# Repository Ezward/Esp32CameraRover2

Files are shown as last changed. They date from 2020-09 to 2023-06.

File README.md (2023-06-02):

# EzRover

- [Description](#description)
- [Status](#status)
- [The Software](#the-software)
    - [Rover Firmware](docs/rover_firmware.md#the-rover-application)
    - [Web Application](docs/web_client.md#the-web-client)
      - Here is a [video](https://youtu.be/yN2ya2mlBNU) that describes the web application.
- [The Hardware](docs/building_the_rover.md#building-the-rover)
- [Todo](docs/todo.md#todo)
- [Tags](docs/tags.md#tags)
- [Setup](#setup)

## Description
EzRover is not a sketch; it is a framework for powering cheap, capable and extensible differential drive robots.

The repository includes a C++ application that runs on the rover and a JavaScript web application that is served by the rover and is used to command the rover and to receive and visualize video and telemetry.  

The framework implements important robot primitives in the C++ application such as a websocket command protocol, closed loop speed control, pose estimation and go to goal behavior.  These primitives are implemented in C++ and run on the rover so they run fast and with low latency.

In addition, the rover serves it's own JavaScript web application which is used to calibrate and command the rover and to visualize video and telemetry from the rover.  The JavaScript web application is a distinguishing feature of this framework.  It can be used to extend the rover's capabilities using a friendly programming language (JavaScript) and powerful technologies like OpenCV.js and Tensorflow.js.

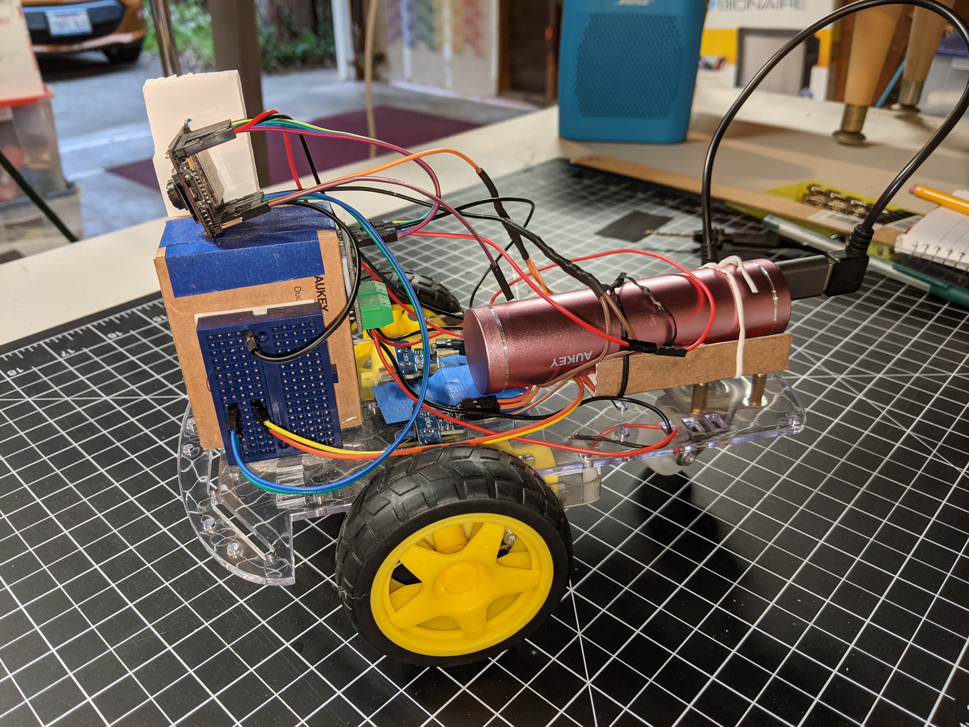
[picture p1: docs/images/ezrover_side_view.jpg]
EzRover side view


This repository includes the parts list and a set of instructions for building an inexpensive differential drive robot using an ESP32Cam micro controller, an inexpensive motor controller and a commonly available Robot Car chassis.  The result is a cheap, capable, extensible robot that can be used by hobbyists or in school settings for experiencing and learning about robotics.
- Sub-$40 bill of materials, no 3D printing and little or no soldering
- Closed-loop motor control, pose estimation, go to goal and path following.
- Remote control using a First Person View video streaming and game controller or mobile phone
- Extensibility via JavaScript, OpenCV and Tensorflow

So two important requirements are:
- The robot must be inexpensive
- The robot must be easy and safe to build

The capabilities listed above then create some other requirements;
- The robot must have it's own battery so it can operate remotely and untethered.
- The robot must have a camera to enable a first persion view for the remote operator and as a sensor for autonomous navigation.
- The robot must have odometry (using wheel encoders) for precise control of speed, trajectory and distance.
- The robot must have wifi communication to enable effective remote control from a computer or cell phone.

The chassis for the robot is a very commonly available kit that includes two dc motors, two wheels, a caster wheel and a clear plastic chassis/platform to mount everything on.  Construction is very simple.  The only soldering required is to attach 2 wires to each of the 2 motors and there are even ways of avoiding that.  

The other nice thing about these kits is that they come with wheel encoder disks; we can add two optocouplers to enable precise odometry for the robot, which is important in a number of scenarios.

The Esp32 Cam was chosen because it is a very inexpensive microcontroller that includes a camera, bluetooth and wifi.  It also comes with the header pins pre-soldered, which eliminates the need for a lot of soldering.  This is nice for beginners and for scenerios where a hot soldering iron is undersirable.  

Wiring of the robot is done using inexpensive and easy to find jumper wires with pre-crimped dupont connectors.  For the most part, we have chosen components that have pre-installed header pins so we can just connect to them using these pre-fabricated jumper wires.  This makes wiring primarily solderless.  The possible exceptions to this are the dc motors.  Each motor has two terminals that need wires connected. It turns out that soldering lead wires to such terminals is really easy, even if this is your first time using a soldering iron.  If the robot is to be assembled in a class room setting, then the wires could be pre-soldered by a teacher.  However, there are alternatives; motors can be purchased that have the lead wires presoldered.  These tend to be a little more expensive are are rarely found in a complete kit, but they can be purchased separately.

## Videos
Here a some videos that show the EzRover and web application is action:
- [EzRover 01 Introduction](https://youtu.be/yN2ya2mlBNU)
- [EzRover 02 Calibration](https://youtu.be/ciDCUUx8MXI)
- [EzRover 03 Go to Goal](https://youtu.be/_eKCqswX5D0)
- [EzRover 04 Go to Goal](https://youtu.be/TjE9ceNOTJE)

## Contributing
There are lots of ways to contribute to this project.  First, clone the repo and try it out.  If you have ideas for cool features please add a Feature Request to issues; I really want to know how you would like to use this project.  If you build the project and find any bugs, please add a bug issue.  If you want to add to the code or fix a bug, please clone the repository and make a pull request.  If you like robots and JavaScript, please star this repository; that will help us a lot.  Thanks!

## The Software
The rover software is really two big pieces; 
- The [rover code](docs/rover_firmware.md) that controls the motors and the camera runs in the ESP32 microcontroller is written in C++ (Arduino flavor).
- The client [web application](docs/web_client.md) that is used to drive the rover and view camera video runs in a browser and consists of an html file, a few css files and many JavaScript files.  

This is not a sketch; it is a framework.  It is a framework for powering cheap, capable, and extensible differential drive robots.

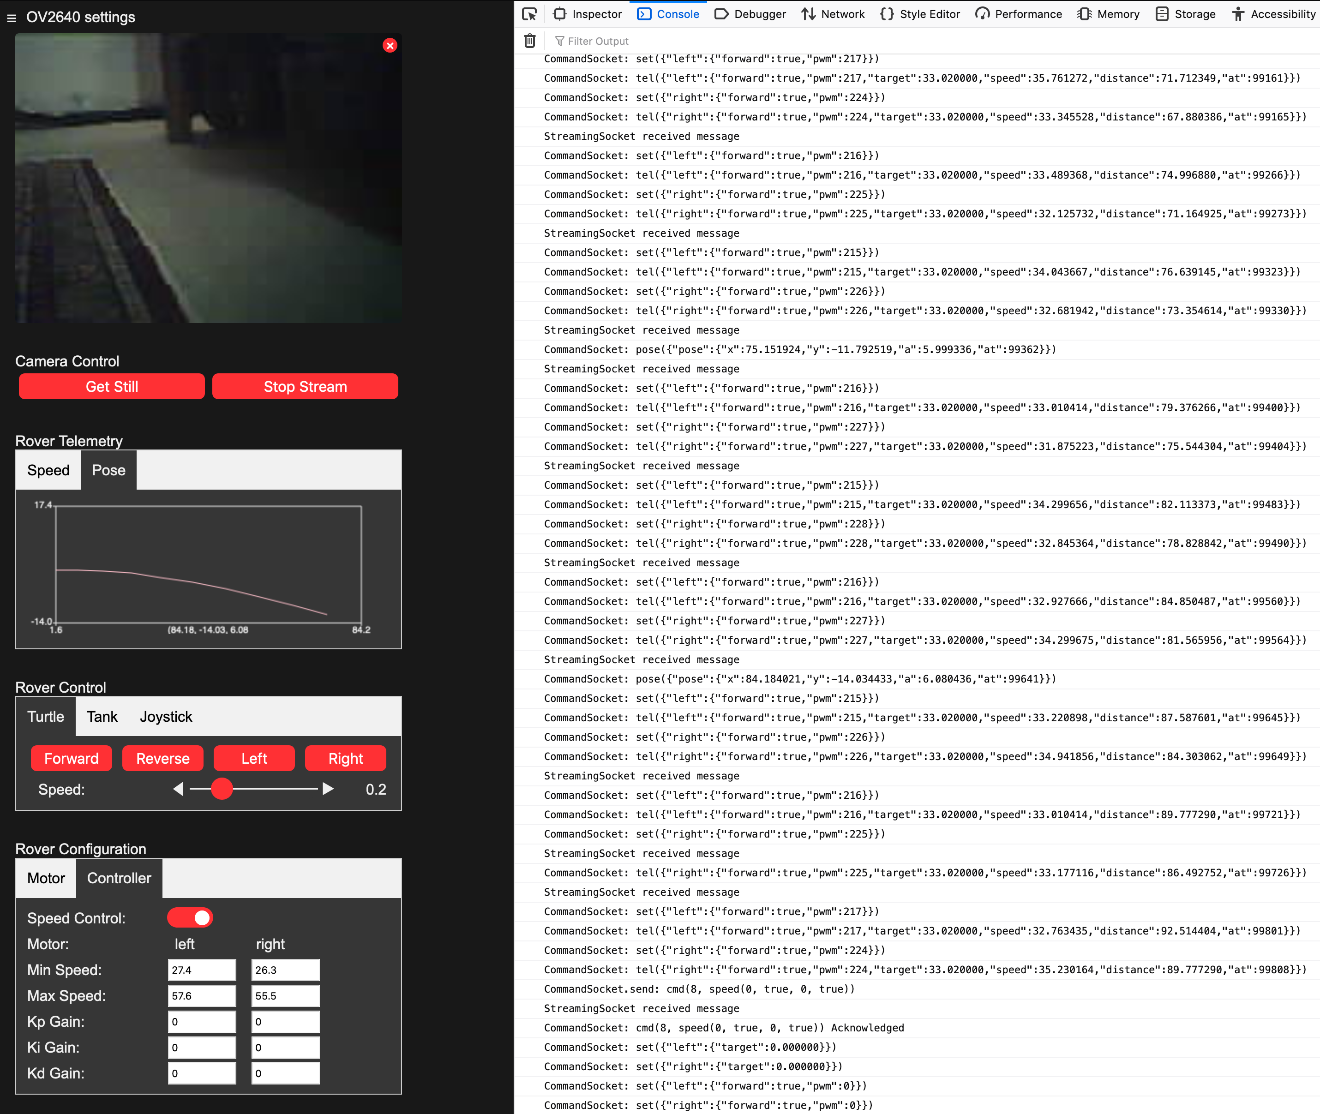
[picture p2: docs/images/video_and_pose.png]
Rover application showing video and pose telemetry


## Status
Latest code has a pretty nice web ui and decent closed-loop speed control and go-to-goal behavior.  My thinking on the project and where it can offer value or provide a differentiated capability has evolved.  Originally I wanted to create the lowest-cost robot capable of competing in a [DIYRobocars](https://diyrobocars.com/) race.  The current [Minimum Viable Racer](https://diyrobocars.com/2018/11/23/updated-minimal-viable-racer-to-use-latest-openmv-linear-regression-code/) is based on the OpenMV Cam, which is a super-nice intelligent camera with onboard compute.  A Minimum Viable Racer would cost a little under $100 to build.  I think this project could be used to create a MVR for about $40.  I still think that is true, but think there is another place we can get to that offers a broader value.  I think this project can become a cheap robot platform that provides solid primitives (speed control, pose estimation, go to goal, command protocol, telemetry and camera streaming) in a self-hosted web application that is extensible in JavaScript.  Cheap, Capable, Extensible.  

### Cheap
This project specifies a hardware BOM that is easy to get, easy to assemble and **costs under 40$** USD.  It does _not_ require a 3D printer.  It can be built with minimal or no-soldering.

### Capable
Ultimately, I would like this project to enable autonomous robotic capabilities.  It is common to see inexpensive robots based on an Arduino Uno or Nano and the same or similar rover chassis and motor controller as this project uses.  These are basically the same cost to build as this project.  They may add a set of IR sensors and provide a line-following behavior.  Or they may provide an ultrasonic sensor and provide an obstacle-avoidance/random-walk kind of behavior.  Sometimes they will provide a bluetooth adapter and a mobile app so the robot can be driven by the user with a mobile phone.  These are all good robots and I would recommend building one or another.  However, none of these are truly autonomous; the line following robots require that you draw lines for them, the obstacle-avoidance robots don't know where they are or where they are going; they just avoid stuff, and the remote control robots require you to drive them.  Autonomous robots require more capable sensors and must be able to estimate and control their position.

- **Camera**: In it's simplest use, streaming video from the camera allows the rover to show a First Person View, FPV, and facilitates remote teleoperation capability.  When combined with computer vision algorithms, a camera equipped robot can execute many autonomous behaviors; line following, lane keeping, obstacle detection, image recognition, camera SLAM and many more.  

- **Wheel Encoders**: integration of wheel encoders for feedback and a kinematic model enables 3 important robot capabilities:
  - speed control: precisely control the speed of the rover under program control
  - pose estimation: understand the position and orientation of the robot as it moves
  - go-to-goal behavior: navigation to a specific location under program control.
- **Wifi** and **web** connectivity: This allows the robot to be controlled over the web; commands can be sent and telemetry can be received.  This is the key to extensibility.
  - command protocol
  - rover telemetry

### Extensible
It's not a sketch, it's a framework for differential drive robots. 

The basic capabilities of the rover are built-in; speed control, pose estimation, go-to-goal behavior.  Those are written in C++ and execute directly on the rover's microcontroller.  Because we have chosen a microcontroller with WIFI and HTTP, the robot can self-host it's own web application and user-interface. This is where a lot more capability can be added in an easy to use language; JavaScript.  Since the rover serves it's own web application, the robot can be run without the need to install a separate client application; just open the application in any browser on a computer or mobile phone.  The application is written in it's own framework with minimal required dependencies so it is very easy to build and debug using standard browser development tools.  

The rover web application can send commands to the rover and it can receive telemetry from the rover so it knows the rover's state.  It allows the rover to be driven by keyboard, game controller or algorithmic control.  There is a graphics library that plots telemetry and position in real-time.  Detailed telemetry can be viewed in the browser's console.  The rover can also stream video from the camera to the rover application.  With powerful JavaScript libraries, like OpenCV.js and Tensorflow.js, computer vision and deep learning algorithms can be run against the camera input.  By leveraging the built-in speed control, pose estimation and go-to-goal primitives, higher-level behaviors can be created like goal selection, path planning, sign-recognition and real-time obstacle detection and avoidance; the building blocks of an autonomous vehicle. 

- Self-hosted **web application**
- Extensible with **Javascript**
  - **OpenCV**.js
  - **TensorFlow**.js
- Debuggable: since much of the robot's code is in JavaScript, the browser's **development tools** can be used to debug.

#### Useful Extensions
These would be great things to add to the the JavaScript application.
- OpenCV.js camera calibration
- OpenCV.js camera line following
- Camera lane keeping (OpenCV.js or TensorFlow.js)
- Path representation and Pure Pursuit path following
- Map representation and path planning
- Traffic sign and traffic light recognition (TensorFlow.js)
- Obstacle recognition and avoidance (Tensorflow.js)

### What would you like to see?
- Add an enhancement request to the github issues.  That can begin the discussion.  It would be great to know how you want to use the rover.
- Before you add a new issue, please search the current issues to see if there is one that covers your concern.  If there is, add to that discussion.  Thanks.

## Setup
I'm using Visual Studio Code and the Platform I/O plugin for embedded development.  It's nice because it can handle the C/C++ code and the HTML/CSS/JavaScript code all in one IDE.
- Install Visual Studio Code: https://code.visualstudio.com/
- To get type-checking of JavaScript in Visual Studio Code (code is JavaScript with JsDoc that can be type-checked):
  - Install nodejs: https://nodejs.org
  - Install TypeScript: https://www.typescriptlang.org/download
- Install Platform I/O into Visual Studio Code: https://platformio.org/platformio-ide
- git clone the repo to your local machine
- open the cloned project folder in Visual Studio Code

See [Rover Firmware](docs/rover_firmware.md) for a detailed explaination of setup and code building.

NOTE: Currently I do not have a Windows batch scripts that are equivalent to the Bash shell scripts in the tools folder that are used to bundle the client assets into the rover firmware.  You could do this in a Linux shell if you have installed Linux Subsystem for Windows.  It may also work in the Git for Windows shell or Cygwin. You can also run a VM.  https://itsfoss.com/run-linux-commands-in-windows/  Lastly, if you create equivalent batch scripts, please think about opening a pull request so the community can use them.  Thanks.

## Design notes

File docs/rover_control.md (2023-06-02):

## Rover control
Controlling (driving) the rover is done with the web application.  There are 4 control modes;
- ***Turtle Control*** : This is is like a Logo 'turtle'; you can move forward, backward, turn left and turn right.  This is done with 4 buttons in the web UI.
- ***Tank Control*** : In this mode, each wheel is controlled separately and can go forward or backward.  This is done using a connected game controller and two of the analog axis, one for each wheel (see how to connect a game controller to your browser below).
- ***Joystick Control*** : In this mode, the rover is controlled with one analog joystick (or one for steering and one for throttle) using a connected game controller (see how to connect a game controller to your browser below). 
- ***Go to Goal*** : In this mode, you provide an (x,y) position and the rover drive's itself there and stops.

- TODO: document how to get wifi address of ESP32 (turn off wheel encoders and get address from serial monitor; use wifi router to fix rover's DHCP ip address in the router)

### Turtle Control 
In 4-button Turtle control mode, the rover has 4 movement commands; forward, turn left, turn right, and reverse.  The speed command sets the speed of the motors.  So when a direction command is given, the speed is based on the most recent speed command.  Finally there is the stop command, which will stop the motors.  
- forward
- turn left
- turn right
- reverse
- stop
- speed

Here is a video that demonstrates [Turtle mode](https://youtu.be/yN2ya2mlBNU) control.

Turtle Control is simple to understand and makes it easy to plan a route; it can also be implemented simply with UI buttons or a keyboard.  The left-turn and right-turn commands are really 'spin' commands; the rotation is around the center of the robot, between the two wheels.  If effect, it is like a 'turtle graphics' kind of control.  So Turtle control mode allows the bot to go forward or backward in a straight line and to spin left or right.  Smooth turns are not really possible, but must be broken up into short strait lines connected with small turns (like approximating a circle with a polygon).

The browser application provides 4 buttons in the UI to send these commands to the rover.  When a direction command is sent by clicking a direction button in the browser application, the command is sent and the button turns to a 'stop' button and the other 3 direction buttons become disabled until the 'stop' button is pressed.  This makes it visual obvious that the user should send a 'stop' command between movement commands.

In addition, the browser application binds the arrow keys on the keyboard of a desktop or laptop or Chromebook to send these commands to the rover.  The arrows keys are mapped as you might expect; up-arrow = forward, left-arrow = turn left, right-arrow = turn right, and down-arrow = reverse.  The application code always inserts a stop command between movement commands to make sure there is no attempt to change direction dramatically (like directly from full forward to full reverse) that has the possibility of damaging the motor's gears.

This is the default mode and works with any desktop or mobile browser.

### Tank Control
In tank control mode, each motor is controlled separately and can go either forward or backward with a specified speed.
- left forward/reverse
- right forward/reverse

This mode is meant to be used with a gamepad that has at least two analog joystick controls, like an XBox One controller or a Playstation 2, 3, or 4 controller.  Typically the left joystick's vertical axis would be used to drive the left wheel; push forward to turn the wheel forward, pull back to turn the wheel backward.  The speed of rotation is determined by how far the stick is moved.  Similarly, the right joystick is generally used to control the right wheel.

Because of the analog nature of the controls, much smoother movements can be created using this mode.

Tank control is enabled when a gamepad with at least two joysticks is connected to the computer that is running the browser application and a button or joystick on the gamepad is pressed or moved.

### Joystick control
In joystick control mode is meant to be used with a gamepad that has at least one analog joystick (the existence of 2 'axes' is assumed to mean one joystick).  One axes controls the forward/reverse speed (push forward to go forward, pull back to reverse) and the other axes controls turning (push left to turn left, push right to turn right).  The speed is determined by how far the joystick is pushed forward or backward and the angle or the turn is determined by how far the joystick is moved left or right.
- forward/reverse
- left/right

Joystick mode is perhaps the most natural driving mode.  

Note that it is also possible, on a gamepad with two analog joystics, to map the vertical axis of one joystick for forward/reverse and the horizontal axis of the other joystick for left/right turns.

Joystick control is enabled when gamepad with at least one analog joystick is connected to the computer that is running the browser application and a button or joystick on the gamepad is pressed or moved.

### Browser Gamepad support
Tank Control and Joystick Control require a gamepad connected to the machine running the browser application. Detection of the gamepad controller and configuration of the axes is done using the HTML5 gamepad API.  To make this mode available, you must first connect a gamepad controller that has at least one analog joystick for Joystick Control or two analog joysticks for Tank Control (actually, the existence of 2 'axes' is assumed to be a joystick, so 4 axes is assumed to be two joysticks).  Note that after the gamepad is connected to the computer, you must press a button or move a joystick before it is detected by the browser.

This has been tested on the latest Chrome and Firefox 77.01
- Firefox 77.01 on MacOS Catalina 10.15.5
- Chrome 83.0.4103.116 on MacOS Catalina 10.15.5

It appears the Apple Safari does not support the HTML5 Gamepad API.

### Go To Goal
In Go To Goal mode, you input an (x,y) position and the rover drives to that position and stops.  Accuracy depends upon good calibration of motor stall PWM, minimum speed and maximum speed for each wheel.  This capability distinguishes this rover from most other super-cheap rovers.  This is also implemented as a command that can be sent to the rover using JavaScript, and telemetry is returned that tells the web applcation when the goal is achieved.  Once you are ready to start hacking the rover's web applcation, you can use this basic behavior and string many together to get the robot to do more complex behaviors.

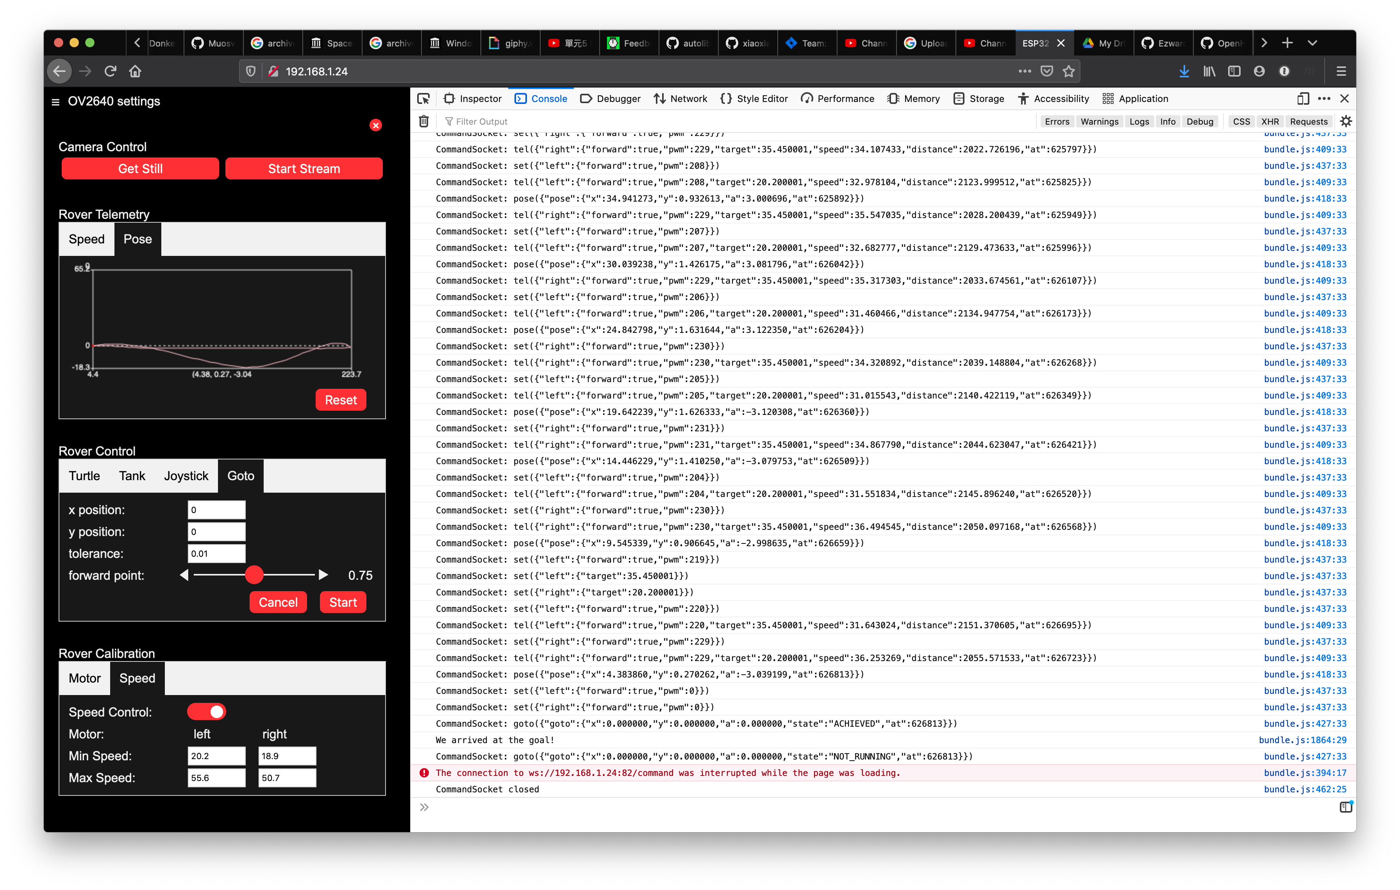
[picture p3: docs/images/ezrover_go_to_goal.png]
EzRover Go to Goal Telemetry


Here is a video that demonstrates the [Go to Goal behavior](https://youtu.be/_eKCqswX5D0) in action.  Here is another with side-by-side video of [EzRover and the telemetry](https://youtu.be/TjE9ceNOTJE) on the web application.

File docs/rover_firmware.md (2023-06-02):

## The Rover Application
The rover code (this is what I'll call the code that runs on board the ESP32) runs in the ESP32 Cam microcontroller.  It is written in Arduino flavor C++.  It includes 3 big pieces of functionality;
- The web server code
- The camera code
- The rover code

***The ESP32 Application Structure***
- WebServer - handle camera configuration requests
- Streaming Server - receive rover commands, stream image frames
- Camera - configure and read frames from the ESP32 Camera
- TwoWheelRover
    - CommandProcessor - parse rover commands and execute them on the rover.
    - DriveWheel x2
        - Motor - send control signals to the motor via a L9110s motor controller board
        - Encoder - read wheel revolutions using optical-interrupter board
        - SpeedController - control wheel speed using a software PID controller
    - Pose Estimator - continually update the rover's idea of it's position and orientation as it moves.
    - GotoGoal Behavior - Use speed control and pose estimation drive the rover to a given (x,y) position

Much of the camera code in `src/camera` is adapted from the ESP32 Cam `CameraWebServer` demonstration sketch provided with the ESP32 Cam Arduino framework.  It would be worth your time to get that demo application running on your ESP32 Cam before you attempt to build the rover and run the rover application.  That will give you the opportunity to learn how to install the necessary libraries and how to upload programs to the ESP32 Cam via a USB-to-Serial adapter board.  I recommend the [article](https://dronebotworkshop.com/esp32-cam-intro/) and [video](https://www.youtube.com/watch?v=visj0KE5VtY) from The Dronebot Workshop.  He provides an excellent, thorough description of how to setup the software and upload and run the demonstration script.  NOTE: after showing how to run the demonstration sketch, he goes into a section of how to add an external antenae to the ESP32 Cam; you do NOT need to do that for this project.

NOTE: On startup the rover tries to connect to a wifi router using the credentials in the file `wifi_credentials.h`.  That file is NOT checked into the project source.  You will need to create one for yourself that provides credentials to your wifi router.  It is recommended that you do NOT check this into source control.  See the next section, Compiling the Firmware, for the format of `wifi_credentials.h`.

### Compiling the Firmware
See [Firmware Toolchain](./software_setup.md#firmware-toolchain)

This is detailed in in [Firmware Toolchain](./software_setup.md#firmware-toolchain) but it is worth mentioning again here.  The rover needs to compile in the wifi credentials for the wifi it will be operating in.  This is done by putting them in header file that gets included in the compile.
- Create a `wifi_credentials.h` in the `src/` folder - You must add your wifi credentials to this file.  Do NOT check this file into source control.  It should look like this;
```
const char* ssid = "yourwifi";
const char* password = "yourpassword";
```
- Now you can compile the firmware by selecting the check-mark on the toolbar at the bottom of the Visual Studio Window.

### Downloading the Firmware to the Rover
The ESP32Cam has very few available GPIO pins, so the output of the wheel encoder LM393 Optocoupler modules use the Serial TX/RX pins.  That means, in this hardware configuration, we cannot use serial output and wheel encoders at the same time.  So when downloading the firmware to the ESP32, we must disconnect the wheel encoder outputs and connect a USBtoSerial converter.  Once the download is complete, you can disconnect the USBtoSerial converter and reconnect the wheel encoder outputs.  In my prototype, I used a mini-breadboard as a switch-board for this purpose so I did not have to continually disconnect/reconnect dupont wires to the ESP32Cam.  Instead, I use a pair of wires to connect the TX/RX to a mini-breadboard and a pair to the USBtoSerial board and a pair to the wheel encoder outputs.  I connect the the USBtoSerial pair when downloading the firmware.  I connect the wheel encoder pair when I want to run the rover.

- Here is a good video from the Dronebot Workshop which includes a section on how to [download firmware to the ESP32Cam](https://youtu.be/visj0KE5VtY?t=429) 
- To use the serial TX/RX pins for downloading firmware, you must detach the encoder output wires from those pins and connect a USBtoSerial converter (make sure to use a 3.3v serial converter).  The Esp32Cam TX pin (gpio-01) must be connected to the RX pin on the USBtoSerial converter.  The Esp32Cam RX pin (gpio-03) must be connected to the TX pin on the converter.  Connect the GND pin on the converter to a common ground with the Esp32Cam.  Do NOT connect the output voltage from the converter; the converter is powered by the USB connection
- To put the Esp32Cam into programming mode you must also tie gpio-0 to ground.
- Once you have connected the USBtoSerial converter to the TX/RX pins (and to power and common ground), and connected gpio-0 to ground, then you must restart the Esp32Cam so it enters programming mode.
- Once in programming mode you can select the right arrow (->) button on the toolbar at the bottom of the Visual Studio Code window to download the firmware.
- If PlatformIO cannot find the serial port, check your connections.  In particular, make sure you have common ground between the Esp32Cam and the USBtoSerial converter; floating ground will disrupt the serial connection.  Also make sure you have TX->RX and RX->TX connections between the Esp32Cam and the converter.

#### Enabling Serial Output
The ESP32Cam has very few available GPIO pins, so the output of the wheel encoder LM393 Optocoupler modules use the Serial TX/RX pins.  That means, in this hardware configuration, we cannot use serial output and wheel encoders at the same time.  By default the firmware builds with wheel encoders support.  However, if you want serial, you can change the compile options in the platformio.ini file.  This is what it looks like by default: 
```
src_build_flags = 
	-D SERIAL_DISABLE=1
	-D USE_WHEEL_ENCODERS=1
	-D USE_ENCODER_INTERRUPTS=1
    -include arduino.h
```
So you can remove `-D USE_WHEEL_ENCODERS=1` and `-D SERIAL_DISABLE=1`, then the serial output will work, but encoders will not (and so speed control, pose estimation and go to goal behavior will not work correctly).

Note also that if you want to surface information from the rover, you might think about sending this back to the web client via the websocket interface rather than the serial port.

#### Finding the Rover's IP address
You will probably want disable encoders and [enable serial output](#enabling-serial-output) when you first compile and download the firmware, so you can find the IP address of the rover.  When serial output is enabled, the rover will print it's IP address to the serial output on startup.  Alternatively, you can use your WIFI router's administration UI to find the IP address that it assigned to the rover; see your router's documentation.  Once you do that, you can use the WIFI router's administration UI to pin the rover to that IP address, so you will always know the rover's IP when it connects to that router.  That is often called Address Reservation in the router's software; see your router's documentation.

### Firmware Internals
TODO

Here is a slideshow discussing and illustrating the [EzRover algorithms](https://docs.google.com/presentation/d/1t77gDPORG4qcxwhPNWrPlTVjwQWncRw7ujsnF02ZN7E/edit?usp=sharing).

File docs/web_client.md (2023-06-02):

## The Web Client
The rover code not only controls the motors and the camera, it is actually a web server that serves the client web application as html, css and JavaScript.  

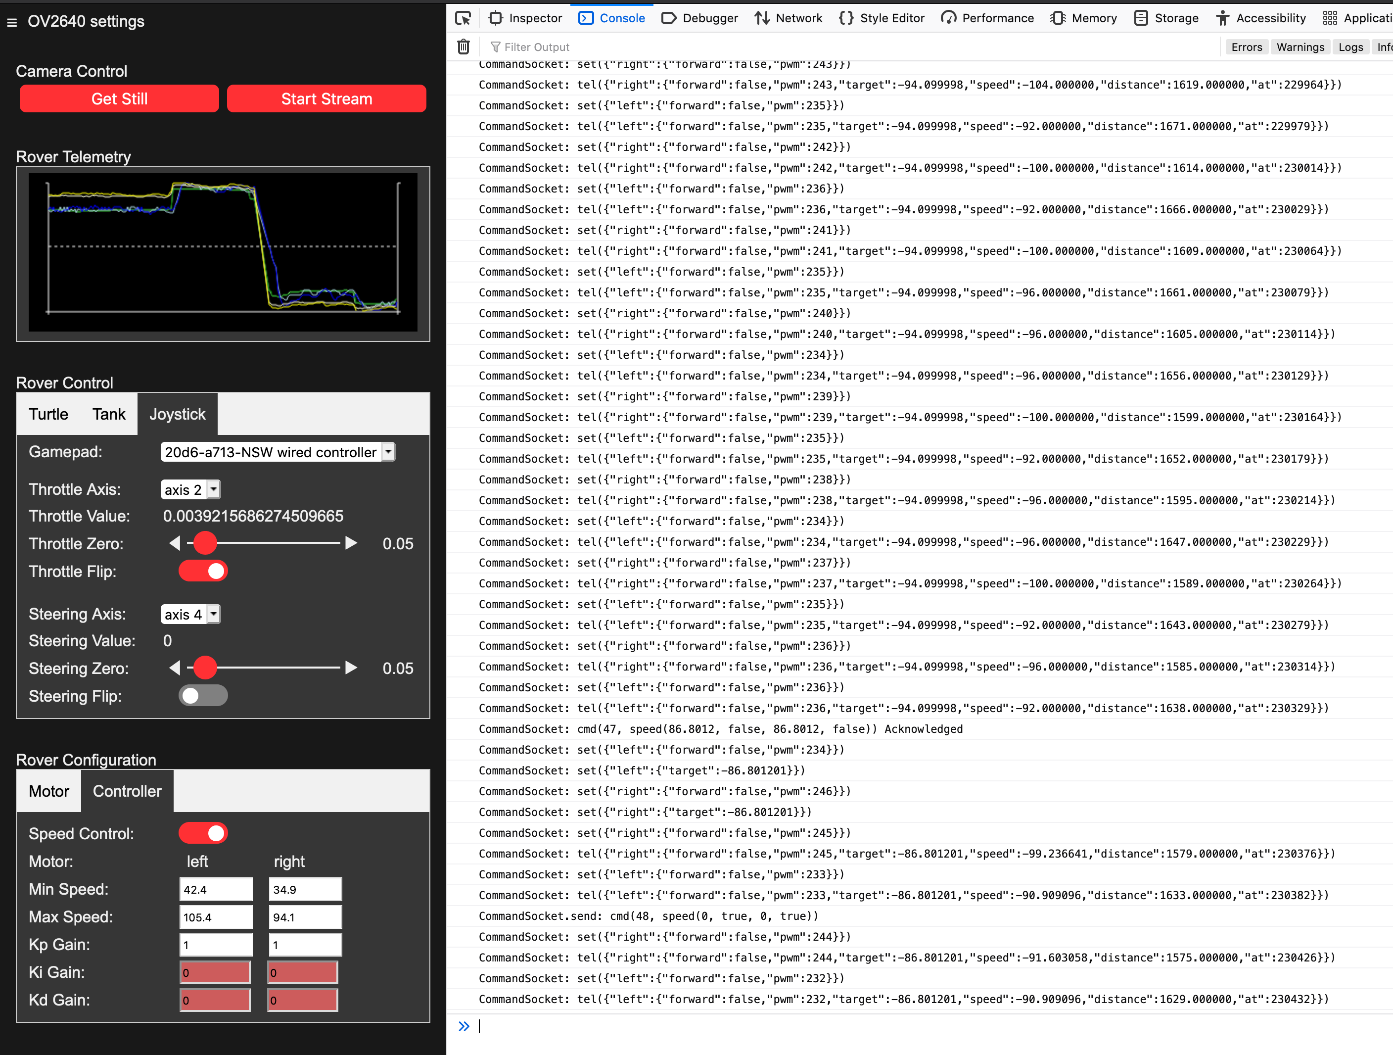
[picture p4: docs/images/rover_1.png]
Rover web application


Most web servers would serve such assets (html, css, javascript) by reading the files from a file system on disk, then sending them via http to the client.  However, we do this a little differently.

The ESP32 Cam does have a 'disk' in that we could use an sd card to hold the files, and we could write the server to read these files, then server them as they are requested.  We actually are not doing it that way because this would add an extra step in getting code to the rover; first we would need to upload the rover code to the ESP32 Cam via the serial connection, then we would need to pull out the SD card, insert it into the computer with which we are editing the code, write the client/ folder to the SD disk, pull out the SD card and reinsert it into the ESP32 Cam.  If both of these steps are not followed, we run the risk of having a set of rover code that is not compatible with the files on the SD card.  

Instead of reading the html, css and JavaScript from the SD card, we turn them into code that is then compiled into a large data array that duplicates what we would have read from disk, but in computer memory.  We then serve that to the client over http.  This requires a bundling and asset conversion step (see below). This done with tool scripts in the `/tools` folder; these steps could easily be added to a build system (like a Makefile).  Another big advantage in our context is that this makes serving those files much faster, since we don't have to read them first from an SD card.

### Asset bundling
The client web application uses a few separate css files and many javascript files.  We want to serve each of these in it's own single request from the client, rather than serving dozens of individual requests for the individual files.  To do that we simply concatenate all the css files into a single css file and all the javascript files into a single JavaScript file.  The bundled css and bundled javascript can then be served in just two requests.  We do this bundling with a bash script.

```
    tools/bundle_assets.sh
```

If you look at the `tools/bundle_assets.sh` bash script you will see that it explicitly copies all .js files to `bundle.js` and all .css files to `bundle.css`.  Note that if you add or remove a .css or .js file from the project, you will need to modifiy the bundling script accordingly.

### Serving assets
The file `client/index.html` is the html app that is loaded when the user hits the root url ('/').  To serve this file, we compress it using gzip and convert the resulting file to an array of bytes in a c-language header file `src/index_html.h`.  There is a bash script that is used to do this process with a single command; `tools/asset_to_c_header.sh`.  It takes two arguments; the first is the name for the asset file to compress, the second is the name of the output header file.  We do the same thing with the bundled javascript and bundled css.  So to create the header files used to serve the web application, run these commands from the root of the project;

```
tools/asset_to_c_header.sh index.html index_html.h
tools/asset_to_c_header.sh bundle.js bundle_js.h
tools/asset_to_c_header.sh bundle.css bundle_css.h
```

Both the bundling and conversion to c-header can be done in one step by calling the tools/bundle.sh script from the root of the project folder.

```
tools/bundle.sh
```

The next time you upload the rover application to the ESP32, the header files will be compiled into the rover application and uploaded with the rest of the rover code.  The are then served from memory (see src/main.c, )

### Debugging the Web Application

The web application is pure html, css and JavaScript, so the developer tools built into your browser (Firefox and Chrome) will do an excellent job of helping you to check your changes and debug the application.  

This can be done by simply opening the web ui served by the rover and then opening the browser developer tools.  However, in some cases it can be useful to debug the web application locally rather than having to upload it to the rover and start the rover.  For instance if you are only modifying css.  

We can serve the web application using a web server on the machine running your IDE.  It uses a version of the html, `index_unbundled.html`, that loads each JavaScript and css file individually, so you don't have to run the bundling steps to see your changes.  In this case the web application does not actually communicate to the rover, but it does allow you to make visual changes to the web application and quickly check them.

If you have installed nodejs as described in [Software Setup](./software_setup.md#client-toolchain) then you have installed a web server that can be used locally.

```
    $ cd client
    $ npx http-server
    Starting up http-server, serving ./

    http-server version: 14.1.1

    http-server settings: 
    CORS: disabled
    Cache: 3600 seconds
    Connection Timeout: 120 seconds
    Directory Listings: visible
    AutoIndex: visible
    Serve GZIP Files: false
    Serve Brotli Files: false
    Default File Extension: none

    Available on:
    http://127.0.0.1:8080
    http://127.94.0.3:8080
    http://127.94.0.2:8080
    http://127.94.0.1:8080
    http://10.0.0.135:8080
    http://172.27.239.20:8080
    Hit CTRL-C to stop the server
```
- Goto the url `http://127.0.0.1:8080/index_unbundled.html` to see the local version of the client app.  You can then open the developer tools using the browser's menus.

>> Chrome developer tool docs: https://developer.chrome.com/docs/devtools/

>> Firebox developer tool docs: https://firefox-source-docs.mozilla.org/devtools-user/

### Web Application UI
The web application UI is organized as follows:

- Camera Control
- Rover Telemetry
  - Motor Telemetry
  - Pose Telemetry
- Rover Control
  - Turtle Control
  - Tank Control
  - Joystick Control
  - Go To Goal
- Rover Calibration
  - Motor Stall
  - Motor Speed

#### Camera Control
This section allow you to show a image or video from the camera and to set many camera settings.  

#### Rover Telemetry
When the rover is driving it sends data back to the web ui.  This section allows you to see two kinds of telemetry.  

The first set of telmetry data shows how fast each motor is turning so you can see how the speed control is operating.  This can help you determine if the calibration values are accurate and/or if the PID values are working well.

The second set of of telemetry that is available is it the robot pose; the estimated position and heading of the robot.  This allows you to see if the pose estimation is working well; is the estimate showing in the rover's path the same or close to what the rover is actually doing?

#### Rover Control
This section provides ways to drive the rover.  There are 4 control modes that the framework supports for driving the rover.

- ***Turtle Control*** : This is is like a Logo 'turtle'; you can use the dialog buttons or the keyboard to move forward, backward, turn left and turn right.  This is done with 4 buttons in the web UI.
- ***Tank Control*** : In this mode, each wheel is controlled separately and can go forward or backward.  This is done using a connected game controller and two of the analog axis, one for each wheel (see how to connect a game controller to your browser below).
- ***Joystick Control*** : In this mode, the rover is controlled with one analog joystick (or one for steering and one for throttle) using a connected game controller (see how to connect a game controller to your browser below). 
- ***Go to Goal*** : In this mode, you provide an (x,y) position and the rover drive's itself there and stops.

See [Rover Control](./rover_control.md) for more details.

#### Rover Calibration
Rover calibration allows you to enter measured values for stall value, minimum speed and maximim speed that the rover has.  These values vary from rover to rover because they are related to the specific motors and battery being used.  Accurately measuring these values makes it so the rover can do a better job of controlling it's speed and turning.  You can find more detailed information on how to measure and set these values at [Rover Calibration](./rover_calibration.md)

### Web Application Internals and Extension Points

The JavaScript code is organized as follows:

- calibration
  - motor     -- Javascript to calibrate motor's stall characteristics
  - pid       -- Javascript to calibrate the motor's speed range and PID controller
- camera      -- JavaScript for streaming camera images over a websocket
- command     -- Javascript for sending commands to the rover over a websocket
- config      -- Javascript with configuration values
- control
  - turtle    -- JavaScript for driving the rover using turtle movement
  - joystick  -- JavaScript for driving the rover with a game controller
  - goto_goal -- JavaScript for driving the rover to a specific position
- telemetry
  - motor     -- Javascript for drawing the motor speed graph
  - pose      -- JavaScript for drawing the rover's position and orientation graph
- utilities   -- JavaScript for various utilities
- view        -- JavaScript for widgets and view related utilities
- main.js     -- This is the entry point for the web application.

#### Object pattern
If you browse the JavaScript files in the `client/js` folder you will see some common patterns in these files.  Typically there is a constructor function that returns an 'instance' as a simple JavaScript object that has a number of functions exposed.  Something like this;

```JavaScript
function FooBar(giver) {
    
    function foo() {
      _baz(`${giver} gives a foo.`);
      return self;
    }

    function bar(getter) {
      _baz(`${getter} gets a bar`);
      return self;
    }

    function _baz(message) {
      console.log(message)
    }

    const self = Object.freeze({
      "foo": foo,
      "bar": bar
    });

    return self;
}
```

And it can be used like this;

```JavaScript
    const theFooBar = FooBar("Jesse");
    theFooBar.foo();
    theFooBar.bar("James");
```

Note that we commonly create 'fluent' apis; methods return the `self` object so that calls can be chained.  For instace we could rewrite the above example as:

```JavaScript
    const theFooBar = FooBar("Jesse");
    theFooBar.foo().bar("James");
```

This is very simple, vanilla JavaScript that is easy to understand.  The constructor's arguments as well as all local variables and functions are captured in a JavaScript closure.  This allows for powerful patterns; we can truly hide private variables and methods in the object and only expose the public api; private variables and methods start with an underscore (`_`) by convention.  Further the public api can be frozen, as it is in this case, so it cannot be altered in any way.  If we want a singleton object then we can immediately execute the constructor function and set a `const` property, like is done in [`ViewWidgetTools`](../client/js/view/view_widget_tools.js), so there is only ever one of them.  We can pass these objects to the constructors of other objects, thus using composition and dependency injection to organize the application.  If you look at the entry point for the application, [`main.js`](../client/js/main.js) you will see that a lot of what it does is construct objects, very often passing these to other constructors as depedencies, until we have constructed everything we need to run the application.

We chose this very simple pattern because:
- it is vanilla JavaScript; it will run in all browsers and can be debugged in with the browser's developer tools without the need to carry around symbol files.
- it is simple to understand
- it provides powerful enforcement of visibility and immutability of object's api.
- it encourages composition and dependency injection rather that object orientation and inheritance.
- it requires no extra tooling
- because of all of the above it will stand the test of time; bit rot should be not be an issue.

### Common kinds of objects
The kinds of objects/functionality implemented in the JavaScript code fall into a few kinds:

- **models**: Models hold data (also called 'state').  A model may be a simple object with getters and setters or it may be implemented as a [`RollbackState`](../client/js/utilities/rollback_state.js) object which can track which properties have been modified and commit or rollback those modifications.  A model may also use a [`MessageBus`](../client/js/utilities/message_bus.js) to publish a message when any of it's properties change, so that other parts of the application can take an action based on that.

- **view-controllers**: A view-controller manages a part of the view (a part of the ui).  That may be an individual control, like a [range control](../client/js/view/widget/range/range_widget_controller.js), or it may be a more complex piece of ui made of many controls, like the [motor calibration pane](../client/js/calibration/motor/motor_view_controller.js).  View-controllers keep the state of the view in a model (the view state model) and update their elements to match the state if the state changes.  A dom event is emitted when the user interacts with an element controlled by the view-controller; for instance a 'click' event is emitted if a button element is clicked. The dom event is handled by the view controller; it updates its view state model based on the event and if the view state actually changed then any affected elements are redrawn to match the new state.  Redraw always happens using the animation loop so we can gather a number of state updates into a single redraw that is smooth and seemless.

- **widgets**: A widget is an individual ui control, like a button or a graphic image.  This is a special kind of view-controller that deals with a 'single' control that may be made of multiple html elements.  The [`RangeWidgetController`](../client/js/view/widget/range/range_widget_controller.js) is an example of a composite widget; it uses a slider element, a numeric input element and two buttons to manage a numeric value. The [`TabViewController`](../client/js/view/widget/tabs/tab_view_controller.js) is another example of a composite widget; it manages a set of elements that act as tabs; at any time one of the tabs is active and the others are inactive; the view-controller publishes events via a [`MessageBus`](../client/js/utilities/message_bus.js) when the active tab changes so that other controllers can adjust themselve accordingly. 

- **view-managers**: View-managers manage and coordinate several view-controllers.  For instance a tab group will have a view-controller for each pane and another view-controller for the tabs themselves.  The view-manager typically uses a message bus to listen for events from the tab view so it knows which view should be active; it can then activate that pane's view-controller (show it and start it listening for events/messages) and deactivate the other panes' view-controllers (hide them and stop them from listening for events/messages).

- **utilities**: Most other code falls into the category of utilities; typically code that makes doing something a little easier.  For instance the [dom utilities](../client/js/utilities/dom_utilities.js) make it easier to interact with dom elements and the [`ViewStateTools`](../client/js/view/view_state_tools.js) make it easier to maintain and enforce the view state maintained in a ['RollbackState`](../client/js/utilities/rollback_state.js) model.

### MessageBus
We mentioned message bus a number of times when talking about controllers.  A message bus is an object that routes messages between other objects.  Messages are a name and value (data).  An object can subscribe to a message by name on a message bus.  When another object publishes a message with that name on that message bus then the subscriber object's `onMessage()` method is called and passed the message name and value.  It can then do what it wants with it.  More than one object can subscribe to a message and all of them will be notified in the order that they subscribed.  It is possible to use more than one [`MessageBus`](../client/js/utilities/message_bus.js) to different kinds of messages segmented.

The purpose of the message bus is to 'decouple' objects.  When using a message bus the publishing object and the subcriber objects don't know anything about each other except that they are sharing a [`MessageBus`](../client/js/utilities/message_bus.js) object. If we did not use a message bus then the publisher would have to call each subscriber directly; so each subscriber object would have to be passed to the publishing object as a dependency, perhaps through the constructor.  This would tightly fix these relationships.  If another object needed that data then the publisher would have to be modified to use it as a dependency.  This makes the code rigid and difficult to maintain.

### View-controller Life Cycle methods
It is worth doing a deeper dive on view-controllers, since they implement all of the interactivity in the user interface.  View-controllers implement a set of functions designe to move the controller through a life-cycle.

- **Construction**: the constructor function is called and passed the necessary inputs; minimally the css selector(s) necessary to find the elements that the view-controller will manage and sometimes a [`MessageBus`](../client/js/utilities/message_bus.js) that the controller will either subscribe to and/or publish on and sometimes a model that the view-controller will update.  The constructor will create the initial view state model.

- **`attachView()`**: This will use the css selector(s) passed to the constructor to lookup the dom element(s) that it will control.  After this is called then the view-controller's `isViewAttached()` method will return `true` if the dom element(s) could be found.

At this point the controller is constructed and has found the dom elements that it is in charge of.  The next two methods 'activate' the view so it can be used.

- **`startListening()`**:  This will attach dom event listeners to the elements under control and may, if a ['MessageBus'](../client/js/utilities/message_bus.js) was passed to the constructor, subscribe to messages.  In this way the controller is able to react to user events or messages from another object. After this is called then `isListening()` will return `true`.
- **`showView()`**:  This will make the controller's dom elements visible so the user can start interacting with them.  After this is called `isViewShowing()` will return `true`.

Once the view is attached and the controller is listening for events/messages and the view is showing, then the view is up an running.  The user may interact with it, any changes to the view state will be reflected in updates to the view.  

We can deactivate the view by reversing the last two life-cycle steps.

- **`hideView()`**:  This will hide the dom elements that the view-controller manages.  Note that `hideView()` must be called for each time that `showView()` was called (handling 'nested' calls).  The view will be hidden only after the `hideView()` calls balance out the `showView()` calls.
- **`stopListening()`**: This will remove all dom event listeners and unsubscribe from any messages.  Note that `stopListening()` must be called for each time that `startListening()` was called; the event listeners will only be removed when the `stopListening()` calls balance out the `startListening()` calls.

>> Note that if a view is hidden then you should always make sure it is not listening; you don't want the user's input to be handled by hidden ui.

At this point the view is deactivated.  We could reactivate it by calling `startListening()` and `showView()` again.  Or if we are all done with it we can finish the object's lifecycle.

- **`detachView()`**: This will throw away all references to the dom elements, so that the controller object is not hanging onto dom elements that may get destroyed.

Once `detachView()` is called the object can be 'thrown away' or it can be used again provided that the arguments passed to the original constructor are still valid (for instance, the css selectors will still resolved to dom elements).

Note that the api is 'fluent'; most methods return the `self` instance so calls can be chained.  For instance, starting up a view-controller might look like;

```JavaScript
const theViewController = ViewController(containerCss);
theViewController.attachView().startListening().showView();
```

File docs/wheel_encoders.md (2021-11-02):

# Wheel Encoders

Simply speaking, a wheel encoder produces a square wave as the wheel turns and the microcontroller can read the pulses in order to count the number of wheel turns.  The number of pulses per wheel rotation is specific to the wheel encoder and how it is arranged on the motor.    

The commonly available robot chassis uses a yellow gearbox motor and commonly ships with a encoder disk for each motor.  The encoder disk is intended to be used with a LM393 Slotted Optocoupler.  The Optocoupler emits an IR light on one side of the slot and detects the IR light on the other side of the slot.  The encoder disk is secured on the motor's output shaft.  The optocoupler is seated around the edge of the encoder disk, such that when the motor turns the encoder disk (and so the wheel) the encoder disk alternatively blocks and unblocks the IR light.  That results in a logical 0 or 1 respectively in the Optocoupler's output pin. The ESP32Cam can then detect the rising and falling edges of these pulses and keep a count of them.

This kind of encoder is is called a mono-phase encoder because it produces a single square wave.  The number of pulses per wheel revolution depends on the number of holes in the encoder disk.  16 or 20 is common is these cheaper kits.  Let's say it's 20 for illustration; this means that when the wheel makes one full turn, the microcontroller will read 20 pairs of rising/falling edges.  

We can measure the circumference (C = 2*pi*R) of the tire that is attached to the motor; this will be the distance that wheel travels in one revolution.  So the minimum distance that we can detect is one pulse; C / 20.  If we measure the time it takes to get a pulse, then we can calculate velocity.  

### Limitations
This simple kind of mono-phase optical encoder has a number of limitations.  
- 20 pulses per revolution is very low resolution and can lead to very 'noisy' velocity calculations; see how to reduce this [below](#reducing-noise-in-velocity-measurements).  
- It's not possible to determine the direction the wheel is turning just from the encoder pulses.  This can be addressed in software.
- The encoder can produce unwanted pulses when the wheel is stopped.  This happens is the and encoder hole is partially in the optocoupler slot when the rover is stopped; small movements of the rover, which might not even be detectable visually, can produce spurious pulses.  This can be mitigated in sofware.
- It's not possible to determine the absolute position of the wheel using this kind of encoder; we can count ticks since 'start' and so know how much the wheel has turned, but we cannot know in what position the wheel actually is.  This is not a limitation for our application.

### Alternative Encoder Configurations
There are other encoder configurations that address these issues.
- a quadrature encoder is a two-phase encoder; it produces two separate square waves.  The square waves are out-of-phase, but overlap.  This allows the microcontroller to determine what direction the wheel is turning.
- a quadrature encode also naturally handles unwanted pulses that can happen when the wheel stops, but is close to an 'edge'; little movements of the robot will cause pulses even though the robot does not appear to be moving.  In the case of the quadrature encoder, software will read these a series of forward and backward movements and so they naturally cancel out.
- As regards the resolution of the encoder, it is possible to just use a finer resolution encoder wheel, but this has a upper limit.  A better way is rather than put the encoder on the motor's output axle, put the encoder on the motor's main spindle.  Since we are using geared motors, the main spindle spins many, many times in order to turn output axle once.  For instance, if the gear ratio is 100:1, then the main spindle will turn 100 times for each turn of the output.  So if we have and optical encoder with 20 holes on the main spindles, we would get 20x100 = 2000 pulses per wheel rotation.  It is actually more common to have a quadrature encode with one dual-pulse per rotation, so we would get 100 pulses per wheel rotation (although we would get direction and natural rejection of unwanted pulsed from the quadrature arrangement).

Future versions of this project will try gear motors with quadrature encoders, like [these](https://www.amazon.com/Reduction-Multiple-Replacement-Velocity-Measurement/dp/B08DKJT2XF/ref=sr_1_25).  That will likely require a different chassis.

## Handling Direction and Momentum
The simple optical encoders that come with the cheaper robot chassis are 'mono-phase' encoders; they produce a single square wave.  It is not possible to determine if the wheel is moving forward or backwards simply by looking at the pulses.  However, since we are controlling the motors, so we know which direction we told them to turn.  So each wheel keeps a value of -1, 0, or 1 to indicate if the wheel is moving backwards, is stopped or is moving forwards respectively.  When a pulse is emitted by the encoder, this value is added to the 'count' of pulses.  So if we told the motor go in reverse, then -1 will be added, thus decrementing the count.  If we told the motor to go forward, then 1 will be added, incrementing the count.  Finally, if we told the motor to stop, then zero will be added; thus we do not change the count when we've told the motor to stop.  

This last part, where we add zero when we believe the rover should be stopped, also handles rejection of the spurious pulses we can get if the encoder wheel stops with a hole 1/2 in and out of the optocoupler slot.  However, this causes another small problem; the rover does not immediately stop when we tell the motors to stop; there is some momentum that make the wheel turn a little more.  The same thing can happen when reversing direction; it takes a small time for the rover to stop moving in it's original direction and start to move in the opposite direction.  This frameworks adds code that makes the encoder continue to integrate in the original direction for a short time after being stopped or reversed. You can change this for your rover by editing config.h.

```
const unsigned int CONTROL_SETTLE_MS = 20;     // number of milliseconds after changing direction that we
                                               // we continue to integrate encoder ticks in the prior direction
                                               // in order to handle inertia.
```

## Reducing Noise in Velocity Measurements

We want to run speed control and pose estimation as fast as we can so we can respond quickly to perturbations.  However, because of the low resolution of the optical encoders used in this robot, we would often get zero or one ticks in the fixed-time window used to do speed control and pose estimation.  This meant the change in velocity between frames was very often 100%; very noisy.  By adding code to require a minimum tick count before doing pose estimation or speed control, everything got much, much better.

We found that the 'noise' was really about too few ticks in a fixed-time sample, so a change of just one tick would create a large apparent change in velocity.  Think about a constant velocity where in a fixed-time sample we would get 2.5 ticks on average.  What really happens is that in one sample we will get 2 ticks, in the next 3 ticks.  If we calculate velocity using this small fixed window, then it will vary from sample to sample greatly.  But if we were to force every sample to have at least 3 ticks, then the time-window is what is varying. The system time is much higher resolution that the tick rate.  That is what reduces the noise in this case.  

There can be false triggering of the encoders that can add noise, but that usually happens 'at rest' when the robot is supposed be stopped; sometimes it stops when the edge of an encoder 'slot' is in the optical path and any slight vibration of the robot can cause rising and falling edges.  That can be eliminated by disabling counting of ticks when the pwm value is zero (so when you want the robot to be stopped, don't count encoder ticks). Noise caused by loose connections can be eliminated by checking and securing all electrical connections.

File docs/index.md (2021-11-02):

# EzRover : Cheap, Capable, Extensible Differential Drive Robots

EzRover is a framework for creating cheap, capable and extensible differential drive robots.  The repository includes a C++ application that runs on the rover and a JavaScript web application that is served by the rover and is used to command the rover and to receive and visualize video and telemetry.  Finally, the repository includes hardware specifications and assembly instructions for a inexpensive (less than $40), easy to build (little or no soldering) robot based on the Esp32Cam microcontroller.

The framework implements important robot primitives in the C++ application such as a websocket command protocol, closed loop speed control, pose estimation and go to goal behavior.  These primitives are implemented in C++ and run on the rover so they run fast and with low latency.

In addition, the rover serves it's own JavaScript web application which is used to calibrate and command the rover and to visualize video and telemetry from the rover.  The JavaScript web application is a distinguishing feature of this framework.  It can be used to extend the rover's capabilities using a friendly programming language (JavaScript) and powerful technologies like OpenCV.js and Tensorflow.js.

EzRover side view

- The Software
    - [Rover Firmware](./rover_firmware.md#the-rover-application)
      - Here are slides describing the [EzRover underlying algorithms](https://docs.google.com/presentation/d/1t77gDPORG4qcxwhPNWrPlTVjwQWncRw7ujsnF02ZN7E/edit?usp=sharing).
    - [Web Application](./web_client.md#the-web-client)
        - Here is an [EzRover introduction](https://youtu.be/yN2ya2mlBNU) video.
        - [Rover Control](./rover_control.md#rover-control)
          - Here is a video describing the  [EzRover calibration](https://youtu.be/ciDCUUx8MXI) process.
          - Here is a video showing the [EzRover Go to Goal](https://youtu.be/_eKCqswX5D0) behavior.
- [The Hardware](./building_the_rover.md#building-the-rover)
- [Todo](./todo.md#todo)
- [Tags](./tags.md#tags)

Web Application Video and Pose Telemetry

## Videos
Here a some videos that show the EzRover and web application is action:
- [EzRover 01 Introduction](https://youtu.be/yN2ya2mlBNU)
- [EzRover 02 Calibration](https://youtu.be/ciDCUUx8MXI)
- [EzRover 03 Go to Goal](https://youtu.be/_eKCqswX5D0)
- [EzRover 04 Go to Goal](https://youtu.be/TjE9ceNOTJE)

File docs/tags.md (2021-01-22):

## Tags
- **v0.2**
  - Serve gzipped html/css/javascript page.
  - Control rover with keyboard.
  - /rover handler adds command to a queue and returns immediately to caller.
  - FreeRTOS background task is used to process the command queue.
- **v0.3**
  - /capture to get a single image based on the current camera configuration
  - /control to set the camera configuration
  - /status to get the camera configuration
  - /health to get the health of the server
  - /stream returns a 501 Not Implemented
  - ported the camera properties code from the canonical Esp32CameraWebServer sample and adapted it to the ESPAsyncWebServer.
    - TODO: need to port the code that calculates the best frame buffer size; current code uses a hard coded value.
    - TODO: currently gets a lot of brownouts when starting up; probably asking for image too early.
  - update web app to continuosly call the /capture endpoint in order to simulate streaming (see downsides in notes above).
- **v0.4**
  - implemented WebSocketsServer to push the image data down to the client.
  - updated client to listen for image data on websocket port 81, then turn it into a blob and assign to img element.  That replaces the prior 'fake' streaming where the client just called the /capture endpoint continuously.  This dramatically increases the framerate and reduces the latency.  It also reduces the connection time for the rover commands, so they are must more immediate and lively.  Probably a lot of that is that this is a totally separate server on a separate port for the images. 
  - web client now opens websocket to start streaming and closes it to stop streaming.  So server starts stream on first pong following connect and stops streaming on disconnect.
  - Fixed crash above 640x480 resolution.  Changed the image capture to take a processing function so that function can operate on the camera's frame buffer is a zero-copy way.  We can now change to any resolution to capture or stream.  We can even change the resolution while streaming.  NOTE: GrabImage still has the bug, but it is not called in this code.
  - At this point I was able to drive it remotely around my house from a browser in my office.  The control structure and latency make it difficult, but it is possible.
  - Added buttons to the web UI to control the rover's direction.
- **v0.5**
  - large changes.  
  - Code reorganization; the index html file was getting very large and unwieldly so it was reorganized.
    - reorganized code to javascript components are in js directory in separte javascript files; same with css.
    - created a version of the index html the references these unbundled assets; this is easier to work with when making changes (and serving from local server rather than the actual esp-32)
    - created a bundling tool that concatenates all the separate javascript files into one file named bundle.js; same with css.
    - modified the index html to include these bundled files
    - modified the main.cpp web server to serve the bundled files.
    - modified the asset to header file tool to handle any kind of file, so we can use it to turn the bundled js and css into header files so they can be served from main.cpp.
  - Added code to support gamepad input
  - Added code and UI to allow the user to choose between turtle, tank and joystick command interfaces.  The actual command code for tank and joystick commands is not yet written.
  - Refactored rover_l9110s.cpp so the command structure can more easily support tank and joystick input by controlling each wheel independantly.
- **v0.6**
    My original hope was to add a PID controller, but I found that
    using a contant increment controller worked well, but was 
    a little slow.  I added a feed-forward mechanism to estimate
    ths initial PWM so that the constant controller would converge
    much faster.  These in combination make it so the rover can
    drive a fairly straight line without consulting distance 
    travelled by each wheel; we can do better if we add lateral
    control using distance travelled.
    The addition of realtime telemetry from the rover back to 
    the web client has been invaluable in figuring out how to 
    make this work.  As a bonus, I've written a system to 
    listen for telemetry, parse it into usable data, then 
    publish it on a MessageBus.  TelemetryListeners then
    subscribe to this data and buffer it.  
    I've also added a charting system that can take the data
    from the TelemetryListeners and plot it in real time
    to a canvas element, so we can now see the speed control
    working graphically in realtime.
  - I suck at tagging.  Ton's of features and code changes have accumulated since v0.5
  - Implemented a websockets protocol for sending text commands for tank and joystick control.
  - Implemented interrupt driven reading of LM393 optical encoders to measure wheel speed.
    - this turned out be be quite a pain because of the limited number of gpio pins on the ESP32Cam.  I basically had to disable serial output so we could then use the pins that would be used for the serial console.  So, we either get speed control or we get serial output.  As you will see below, this is not terrible because I added telemetry from rover to web client via websockets.
  - Implemented a feed-forward step controller to control speed and help rover travel in a straight line at a desired speed.
    - this require a bunch of UI so motor parameters could be configured
      - PWM stall values for each motor, so we know minimum PWM value necessary to get motor turning and we can avoid 'dead zones' where PWM values resulting in voltages too low to turn the motors.
      - minimum speed the motor can maintain
      - maximum speed the motor can maintain
    - there is UI to input PID gain values, but these are not currently used (because we are using a step controller)
  - Implemented telemetry from the rover to the web client over command websocket.  Now we can see the chose pwm, the target speed (if speed control is engaged) and the actual speed.
  - Implemented a system to read motor telemetry in CommandSocket, parse it and publish it.
    - TelemetryListener can listen for telemetry from a specific wheel and buffer data and accumlate useful statistics (min and max).
    - TelemetryListener also publishes a message when data is added; that is critical for plotting telemetry in realtime
  - Implemented a realtime drawing of telemetry to a canvas.
    - LineChart and Axis chart primitives
    - CanvasViewController for binding to a canvas and painting it when telemetry is added.
    - TelemetryCanvasPainter used data in associated TelemetryListeners to draw pwm, target speed and actual speed in realtime.
  - Implemented singleton config object to hold global readonly configuration.
  - Updated range input controls so they have increment and decrement buttons at either end of the slider.  This makes the control much easier to use on a mobile phone.
- **v0.7**
  - This version adds pose estimation and visualization.  In addition, I've improved speed control so it operates more smoothly.
  - Added a Go-To-Goal behavior that can be initiated from the 'Rover Control' tab panel.
  - Added ability to reset the telemetry without needing to reboot the rover.

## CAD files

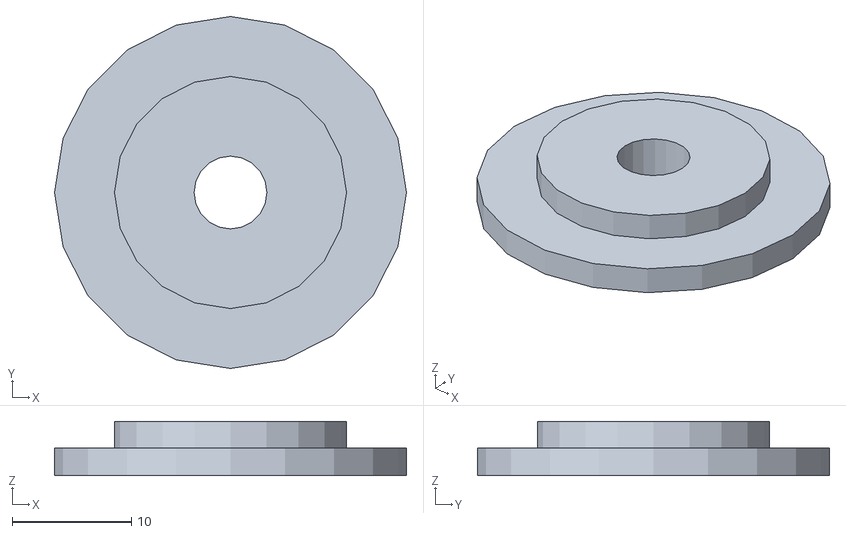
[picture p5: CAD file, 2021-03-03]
3d/gopro_rover_base.stl
29.5 x 29.5 x 4.55

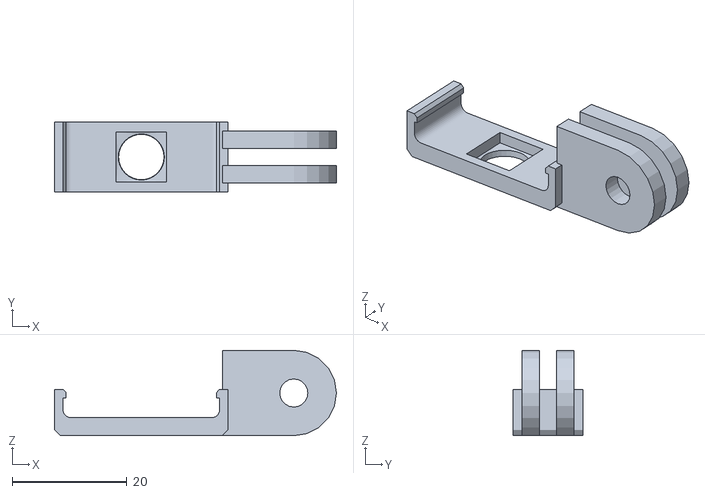
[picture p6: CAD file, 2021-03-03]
3d/Esp32Cam_gopro.stl
49.2 x 12.2 x 14.9

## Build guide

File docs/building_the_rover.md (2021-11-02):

## Building the Rover
The parts are readily available from many suppliers.  I will provide links to Amazon (fast delivery) and AliExpress (low prices), but there are other suppliers that you may prefer.  Think of these links as a description of what you can get and about how much it will cost, rather than a suggestion for any particular supplier.  You may also choose to buy two at a time as this will also save money if you want spare parts or a second robot.  Also, it is sometimes easier to test code on parts rather than a fully assembled robot, so a second set of parts can be handy that way.

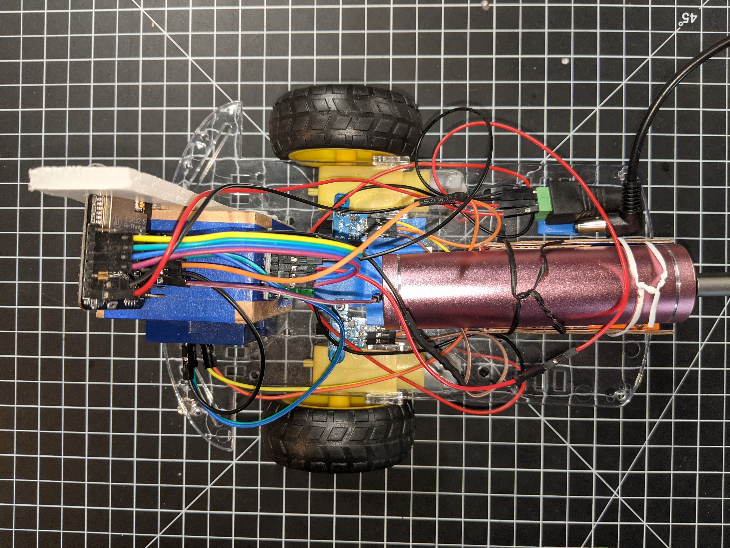
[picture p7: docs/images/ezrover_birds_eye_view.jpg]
EzRover birds eye view


## Bill of Materials

### ESP32 Cam
This is a ESP32-S with an OV2640 camera.
- [Amazon](https://www.amazon.com/SongHe-ESP32-CAM-Development-Bluetooth-Arduino/dp/B07RB2J4XL/ref=sr_1_7)
- [AliExpress]()

### USB to TTL converter
This is used send the program to the ESP32 Cam and read the output of the serial port.  There are a lot of different variations of this kind of board.
- [Amazon](https://www.amazon.com/HiLetgo-CP2102-Converter-Adapter-Downloader/dp/B00LODGRV8/ref=sr_1_4)
- [AliExpress]()

### L9110S DC Motor Driver
This is used to control the two motors of the robot chassis.  It is connected to the ESP32 Cam pins to get 'commands' and to the two DC Motors to provide them with power and control signals.  This is a great chip for controlling small DC motors (and stepper motors) and they are cheaper when you buy several, so if you are interested in building with small DC motors, this is a great, inexpensive motor driver.
- [Amazon](https://www.amazon.com/Comimark-H-Bridge-Stepper-Controller-Arduino/dp/B07WZFGS81/ref=sr_1_14)
- [AliExpress]()

### Smart Robot Car Chassis Kit
These kits can be had from many vendors.  They contain a clear plastic platform with mounting holes, two DC geared motors, two wheels and tires, one omnidirectional caster wheel, two optical encoder disks (for measuring speed; usable if you also get the IR Optocouplers below), a toggle switch, a battery box (which we are not going to use), a little wire and all the necessary mounting hardware.
- [Amazon](https://www.amazon.com/MTMTOOL-Smart-Chassis-Encoder-Battery/dp/B081GYVB6C/ref=sr_1_4)
- [AliExpress]()

These kids generally come with lead wires for connecting the dc motors, but they are not generally pre-soldered to the motors.  That means a little soldering.  That would be a good beginner's soldering task.  But if you don't want to solder at all then there is an alternative; you can purchase the motors with the wire leads already soldered.  They are more expensive, but they do avoid soldering. (see AdaFruit)

Presoldered Motors
- [Amazon](https://www.amazon.com/Gearbox-Motor-Wheel-Arduino-Smart/dp/B07P6QCJPX/ref=sr_1_12)
- [Amazon](https://www.amazon.com/Gearbox-Motor-Shaft-Arduino-Smart/dp/B07P9ZSWBG/ref=pd_rhf_se_p_img_13)
- [AdaFruit](https://www.adafruit.com/product/3777)

### IR Slotted LM393 Optocoupler
These, in combination with the optical encoder discs that come with the Smart Robot Car Chassis Kit, can be used to measure wheel rotation, so you can precisely measure speed and distance travelled.  Note that you can find several different kinds of these slotted Opto-interrupters.  The ones with the header pins on the opposite side of the board from the IR detector slot works best because the pins point 'up' while the slot points 'down'.  On some other kinds, the pins also point down and prevent the module from seating propertly.
- [Amazon](https://www.amazon.com/gp/product/B081W4KMHC/ref=ppx_yo_dt_b_asin_title_o06_s00)
- [AliExpress](https://www.aliexpress.com/item/32773600460.html)

Slotted Optical Disks
If you are not buying a kit, you may need to purchase the disks separately.
- [AliExpress](https://www.aliexpress.com/item/32966921400.html)

### Dupont wires
You should have a mix of male-male, male-female, female-female and 10cm and 20cm.
- [AliExpress](https://www.aliexpress.com/item/1005001705264902.html)

## Instructions
TODO

Smart Car Chassis 1
Smart Car Chassis 2
Smart Car Chassis 3
Esp32Cam Microcontroller
L9110S Motor Controller
LM393 Optocoupler
Dupont Wires
USB Battery

### Wiring

```
                            Left      Right      USB 5V
Esp32Cam         L9110S     LM393     LM393      Battery
--------         ------     -----     -----      -------
GPIO 15   <-----> A1_A
GPIO 13   <-----> A1_B
GND       <-----> GND  <---> GND <---> GND <---> (-) GND
5V        <-----> VCC  <-----------------------> (+) 5V
GPIO 2    <-----> B1_A
GPIO 14   <-----> B1_B
GPIO 3,RX <----------------> OUT
GPIO 1,TX <--------------------------> OUT
VCC       <----------------> VCC <---> VCC
```

EzRover Wiring
ESP32 image (c) 2019 [Robojax.com](https://www.robojax.com)

- Note that this wiring diagram is one way to do it.  It matches what is found in `src/config.h`
```
// pin assignments for motor controller
const int A1_A_PIN = 15;          // left forward input pin
const int A1_B_PIN = 13;          // left reverse input pin
const int B1_B_PIN = 14;          // right forward input pin
const int B1_A_PIN = 2;           // right reverse input pin

// wheel encoder config
const int LEFT_ENCODER_PIN = 3;   // left LM393 wheel encoder input pin
const int RIGHT_ENCODER_PIN = 1;  // right LM393 wheel encoder input pin
```
- The VCC pin of the ESP32Cam outputs 3.3 volts.  We use that to supply the LM393 with 3.3 volts from the Esp32Cam so that the LM393 output pin outputs 3.3 volts, which is compatible with the Esp32cam GPIO pins.  If supply the LM393 with 5 volts, then it's output will be 5 volts and the Esp32 GPIO pins do not tolerate 5 volts.
- Esp32Cam GPIO pin 1 is also the serial transmit pin (TX) and GPIO pin 3 is also the serial receive pin (RX).  We use those pins (and GND) to connect a USBtoSerial converter when we want to download the firmware to the rover or transmit serial output to the host computer.  We can't have both the USBtoSerial converter and the LM393 encoder output pins connected to those pins at the same time.  See [Downloading the Firmware to the Rover](./rover_firmware.md#downloading-the-firmware-to-the-rover) to see how that can be handled.
- Note the wiring from power to L9110S; The right motor is hooked to Motor A terminals of the L9110S and the left motor is hooked to Motor B terminals.  But which terminal from the left motor goes to which of the Motor B terminals?  The order of those connections depends on how the wires to the motor are soldered and because motors can move in either direction, the terminals of the motor are not marked as (+) or (-), so it is hard to determine which side of the motor should be hooked to which terminal on the L9110S.  You will have to experiment to determine which side of the motor goes to which terminal in order to make the wheels move forward and backwards correctly.  

### 3D Printed Camera Mount
This part is optional, but if you have access to a 3D printer it is a nice addition.  This part adapts the Esp32Cam to be mounted on a go pro camera mount.

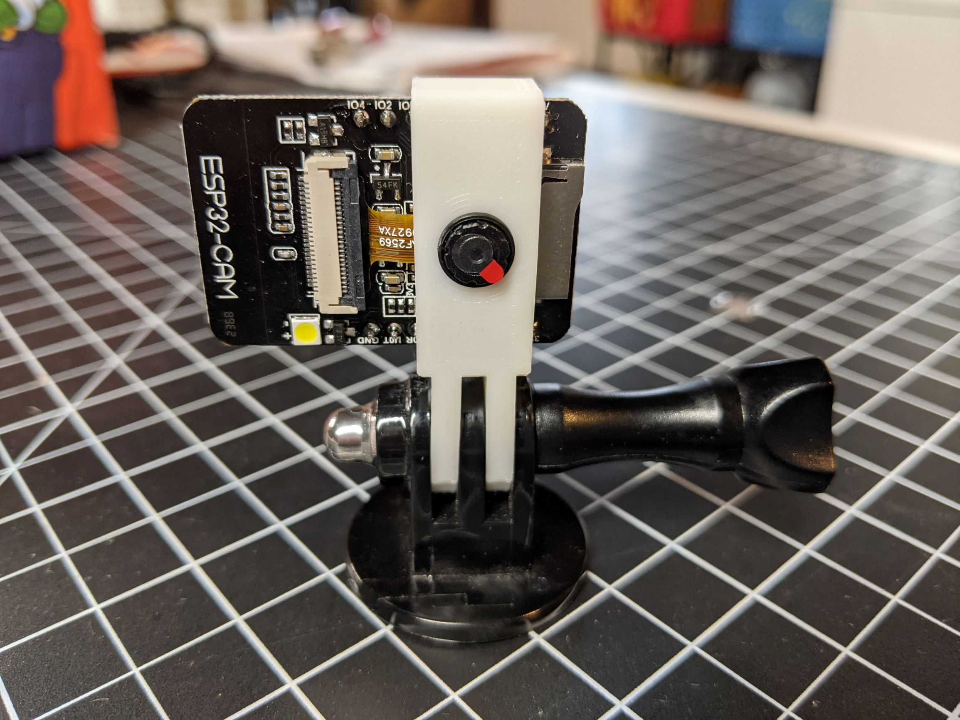
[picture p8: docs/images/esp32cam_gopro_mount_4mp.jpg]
Esp32Cam GoPro Mount


It is a small part and prints very quickly.  Use the stl file in this project or download from [Thingiverse](https://www.thingiverse.com/thing:4781843).

The back leaves all the pins and the reset button exposed so you can continue to develop with the camera mounted.

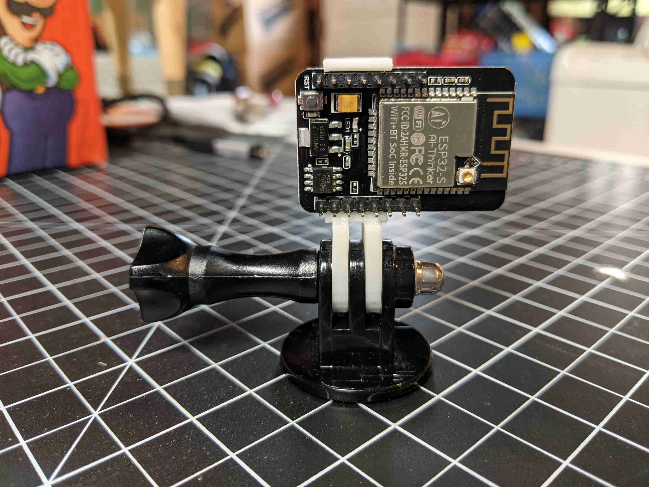
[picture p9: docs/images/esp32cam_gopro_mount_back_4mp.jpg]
Esp32Cam GoPro Mount Back


I printed using PLA, 0.2mm layers and 100% in-fill.  You can purchase the base on Amazon or Aliexpress.
- [Amazon ActionCam Mount](https://www.amazon.com/Alsukeay-Adapter-Compatible-Session-Cameras/dp/B07WWCH6GM/ref=sr_1_37)
- [Aliexpress ActionCam Mount](https://www.aliexpress.com/item/1005002090177047.html)

### Improving the Hardware
- PCA9685 to send pwm to motors.  The PCA9685 would be connected via I2C, so it would save a couple of input pins.  More importantly, we could add additional devices to the I2C serial bus without using any more pins.  That opens up a lot more hardware extensibility by just adding a $4 part.  It also now frees up two pins, so we can move the encoders to those pins and re-enable the serial output.
- IMU to improve dead reconning.  If we add the PCA9685, then one of the sensors we could add to the I2C bus is an IMU.  This could be used to improve dead reconning accuracy.  In particular, it would help mitigate the biggest weakest with the wheel encoders; wheel slip detection.  The IMU, since it measures accelerations, could detect wheel slip.  We would then fuse the output of the IMU with wheel encoders.
- OLED screen so we can show the rover's ip address on startup and other telemetry when running.  Again, if we are using a PCA9685 and the I2C bus, we can add this device to the I2C bus.  This would eliminate the hassle associated with finding the rover's IP address.

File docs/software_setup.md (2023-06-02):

## Software Setup

### Firmware Toolchain
We use the Arduino library for ESP32, but we do so within Microsoft Visual Studio code using the PlatformIO plugin.  Visual Studio Code is much better environment for us than the legacy Arduino IDE because it supports Arduino/C/C++/HTML/CSS/JavaScript development all in one IDE.

- install git if you don't already have it: https://git-scm.com/downloads
- install the Arduino IDE (to get the Arduino compiler): https://www.arduino.cc/en/software
- Install Visual Studio Code: https://code.visualstudio.com/docs/setup/setup-overview
- Install PlatformIO plugin in Visual Studio Code: https://platformio.org/install
- Git clone the code: `git clone https://github.com/Ezward/Esp32CameraRover2.git`
- Use Visual Studio Code/PlatformIO to open the Esp32CameraRover2 folder; platformio should load the project.
- Create a `wifi_credentials.h` in the `src/` folder - You must add your wifi credentials to this file.  Do NOT check this file into source control.  It should look like this;
```
const char* ssid = "yourwifi";
const char* password = "yourpassword";
```
- Now you can compile the firmware by selecting the check-mark on the toolbar at the bottom of the Visual Studio Window.

### Client Toolchain
The good news here is that we don't really need much of a toolchain.  We are using plain HTML, CSS and JavaScript.  We've included some shell scripts to bundle the assets, so no extra tooling is necessary.  However, if you are planning on make changes in the client code then it would be prudent to add a little tooling so that the editor provides much better code completion and type checking.  The JavaScript source is extensively commented with JsDoc comments that include type information and this information can be used by tooling to provide a much better (and less error prone) programming experience.

We use TypeScript to enable code completion and type checking using the JsDoc comments in the JavaScript source.  It is optional but recommended if you intend to modify the client software.  To install TypeScript we first install NodeJS.

1. Install NodeJS
2. Initialize 
3. Install http-server
4. Install TypeScript

#### 1. Install NodeJS
The simplest way to do this is to just use the NodeJS installer from https://nodejs.org/en/download.  If this is the only project that uses NodeJS then that will work well.

I myself have many project that use NodeJS and they all use a different version (of course).  So I have installed a toolchain that allows me to easily use different version of NodeJS.  I am on a Mac, so I use two tools to do this; Homebrew and ASDF.

Macintosh
- Install Homebrew as described here https://brew.sh/
- Install asdf; these instructions are adapted from https://asdf-vm.com/guide/getting-started.html
  - Install coreutils and curl, `brew install coreutils curl`
  - If you don't already have git, then install it with brew, `brew install git`
  - Git clone asdf, `git clone https://github.com/asdf-vm/asdf.git ~/.asdf --branch v0.11.3`
  - follow any addition instructions provided at the end of the installation
- Install NodeJS using asdf
  - Install GnuPG via Homebrew, `brew install gpg`
  - Install the NodeJS plugin, `asdf plugin add nodejs https://github.com/asdf-vm/asdf-nodejs.git`
  - You can now list the available versions, `asdf list all nodejs`
  - Install a version of nodejs, `asdf install nodejs 19.8.1`
- Change into the client folder and set you version of node, `asdf local nodejs 19.8.1`
- Reopen the console so that changes are applied in the new console.

#### 2. Initialize
- Change into the client folder, and initialize the nodejs project, `npm init`
  - This will generate a few questions; take the defaults for package (client), version (1.0.0), description (empty).  When you get to entry point use `js/main.js`.  Take all the defaults after that.

#### 3. Install http-server
- Install http-server so we can run the client locally, `npm install http-server`
- Try running it from within the client folder, `npx http-server`, then open `http://127.0.0.1:8080/index_unbundled.html` in your browser; you should see the client application.  At this point, since we are not actually running this on the robot, git won't completely work, but you can use the browser's developer tools to view the html, css and JavaScript and even use the debugger to set breakpoints.

#### 4. Install TypeScript
- Install typescript, `npm install typescript --save-dev`
- Now when you view the client source in Visual Studio Code it should provide much better type checking and intellisense.
- If you choose to modify the source code (and I hope you do) then this guide will help you add JsDoc comments to your code https://www.typescriptlang.org/docs/handbook/jsdoc-supported-types.html

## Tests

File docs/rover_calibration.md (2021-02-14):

## Rover Calibration
We want to figure out 3 things for each wheel
- The stall value; the fraction of maximum power below which the motor stalls (so this is the minimal power needed to make the motor move).
- The minimum speed; this is the speed at the stall value.
- The maximum speed; this is the speed at full power.

We can observe these values using Turtle control mode.

- Note: You might want to practice this without having to chase around the rover by elevating the rover so the wheels are not touching the ground or rubbing against anything.  That will not yield correct values for running on a floor or carpet, but is is useful for trying out the rover without running around after it

- Here is a video describing the [EzRover calibration](https://youtu.be/ciDCUUx8MXI) process.

- Restart the rover and use a web browser to open the client application.  This should open the application is it's default, uninitialized state.  Specifically, the motor stall values will be at zero, speed control will be turned off and no minimum or maximum speeds are configured.
- Make sure the 'Speed' panel is selected in Rover Telemetry section, the 'Turtle' panel is chosen in the Rover Control section and the 'Motor' panel is chose in the Rover Calibration section.
- First we want to find the stall value.  We can use a 'binary' search kind of algorithm.  In the Turtle panel, set the Speed value to 0.5; the value halfway between stopped and full power.  Now select the 'Forward' button and allow the motors to run for 5 or 10 seconds.  If both wheels move freely for the whole time, then we want to try the value at 0.25; if the wheels to not move, then we want to try the value at 0.75.  We can proceed this way, selecting values midway between known outcomes until we find a value where both wheels move freely, but below which one or both do not move freely.  At point we know know the stall value for each motor _and_ the minimum speed for each motor.  The stall value is smallest 'Speed' value where both motors run freely.  You should write that value down; later we will enter this for 'Left Stall' and 'Right Stall' in the 'Motor' panel of the Rover Calibration section.  You should also write down the left and right minimum speeds; they will be displayed below the telemetry graph in the 'Speed' panel when you have run the motors at the stall value.
- Now we want to find the maximum speed of each motor.  Move the 'Speed' slider all the way to the right so it is set a 1; this is full power.  Now select the 'Forward' button and drive the motors for 5 to 10 seconds.  You can then read the speed of the left and right motors from the 'Speed' panel in the Rover Telemetry section.  Write those down.  Now you might have something that looks like this;  

| |left|right|
|---|----|-----|
|stall |0.75| 0.75|
|minspeed|27.2| 24.3|
|maxspeed|57.7| 54.9|

- Enter the stall values in the 'Motor' panel of the Rover Calibration section.
- Enter the min speed and max speed values in the 'Speed' panel of the Rover Calibration section and set the 'Speed Control' radio button to on. When you select that radio button to on, the speed configuration will be send to the rover and now, when you use the Turtle controls, the 'Speed' slider will choose speeds between min and max, rather that a fraction of overall power.  Further, these values will be used by the 'Goto' control as it moves to the chosen location.

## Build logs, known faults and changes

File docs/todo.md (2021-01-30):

## TODO
These are somewhat ordered, but priorities can change.  The overall goals are: 

1. FPV Rover with keyboard and web UI control. 
   - switch to ESPAsyncWebServer, implement minimal control via /rover endpoint (no UI yet).
   - Add UI to html to control the rover, so it can be controlled from devices that don't have a keyboard (like a phone).
   - Implement streaming video to browser using ~~ESPAsyncWebServer streaming response~~ websockets.
2. Enhanced FPV Rover with better speed and turn control and game controller input for a more natural user experience.
3. Go to goal and path following using dead reckoning.
4. Autonomous lane following.
5. Object recognition and collision avoidance.

x = completed
+ = in progress

- [x] Change to a more performant web server that will allow simultanous streaming of images and processing of rover commands.
- [x] Implement websocket protocol and serve images over websocket (may just be part of improving performance, but down the road we want to also use it so send commands to rover).
- [x] Implement websocket protocol to send commands from browser to rover (rather than HTTP GET api; this forces ordering of commands).
- [x] Implement PWM control for motor speed (and modify UI to support this).
- [x] Implement game controller input (via browser's game control api).
- [ ] Implement authentication so only one person can be driving, but any number of people can be viewing.
- [x] Implement wheel encoders for measuring speed and distance travelled.  
- [x] Implement web UI for calibration of wheel encoders, RPM, distance (required wheel encodes)
- [x] Implement PID algorithm to precisely control speed of motors (and so allow for any turning radius) using wheel encoders (requires calibration of wheel encoders).  Rover should drive in straight line when using the 'Forward' turtle command.  NOTE: Implemented as a feed-forward constant controller rather than a PID controller.
- [x] Implement motor telemetry from rover to web client using websockets (for each wheel: pwm, target speed, current speed, total distance, time in ms) - position and pose TBD, wheel values are done.
- [x] Implement position and pose estimation based on dead reckoning using encoder values.
- [x] Implement pose telemetry from rover to web client using websockets.
- [x] Graph telemetry in web client; 
      - [x] wheel telemetry tab has time as x-axis and dual y-axis; pwm and speed
      - [x] pose and position as (x, y) position of rover and arrow at (x,y) position to show pose.
- [ ] Save settings to flash and load on restart
      - [ ] either send settings to client on connection AND/OR allow client to ask for settings.
- [x] Implement telemetry reset to we can start from zero without hard-resetting the ESP32Cam.
- [ ] Implement commands to allow client to turn on/off or set rate of telemetry based on time.  So ask for zero telemetry, or telemetry every n milliseconds or all telemetry.  Do this for "tel" and "pos".  
  - Modify the TelemetryViewManager to use this to reduce telemetry to the deactivated chart.
  - we may also want to reduce telemetry while streaming video, in order to reduce bandwidth used.
- [ ] Implement commands to turn on/off "set" telemetry.  This is really just needed for debugging.
- [x] Implement UI and command to reset telemetry so we can start from origin without rebooting the rover and reloading the UI.
- [x] Throttle joystick commands such that we don't create a huge queue of joystick commands; 
      - [x] we can check if a command is 'sending' and only enqueue if not sending.
      - [x] we can check if there is already a movement command in the queue and replace it with the latest command so there is only one movement command in the queue.
- [ ] Implement turning arc (radius around instantaneous center of curvature) turtle command and speed control.  Requires slider for turning radius input.
- [ ] Re-implement joystick control to choose a speed (linear velocity) and an turning rate (angular velocity) and use those to calculate the wheel velocities.  Clamp the angular velocity to create some reasonable max turning angle that makes it turn more like a regular car.
- [ ] Add realtime speed/pwm control while driving in turtle mode; add a change handler to the slide and respond to changes in speed slider by sending changes to rover.  
- [ ] Implement PS3 Game controller via bluetooth directly to ESP32 to reduce input latency (necessary for capturing good data for machine learning).
- [ ] Implement CV lane following autopilot running on ESP32 (for Donkeycar kind of track).
- [ ] Implement Neural Network autopilot in TensorflowJS Micro lane following (like DonkeyCar).
- [ ] Implement object detection in browser using TensorFlow.js.  In particular, stop signs, traffic lights, pedestrians and other rovers such that the rover can obey signs and avoid collisions.
- [ ] Implement Neural Network autopilot in Tensorflow Lite Micro for ESP32 for lane following (like DonkeyCar).
- [x] Implement go to goal line follower.  Requires lateral control (line follow) and longitudinal control (stop at goal).  See PurePursuit algorithm.
- [ ] Implement waypoint recorder and associated UI so we can record and playback a path that has been driven ((requires lateral and longitudinal control)).
- [ ] Implement map and path planning such that rover can use autonomous mode to travel from a specified location to another on the map.  Think simulating a 4 block neighborhood with a perimeter road, 4 3-way intersections and a central 4 way intersections and at least one section of a gradual curve (rather than 90 degrees) so we can test smooth turning.
- [ ] Combine path planning, autonomy, obstacle detection and collision avoidance to implment an autonomous package delivery vehicle in a simulated neighbor hood.
- [ ] Implement a version of hardware support that uses a PCA9885 PWM board over I2C to control motor speed.  This only adds $3 to BOM, but frees up lots of pins so we get back serial output from rover even with wheel encoders and we can add other I2C peripherals, like an IMU to improve dead reconning.  Could also add a OLED screen to output the ip address of the rover at startup and other status while running.  So for $3 it adds a lot of flexibility.
- [ ] create a simulator that can serve the client application and simulate the motors and wheel encoders and can server the computer's webcam or a static image for the video stream.  Simulator will need mock wheel and mock encoder so it can simulate wheel speeds based on pwm setting send to the wheel and speed calibration entered in use and sent as commands to the rover.

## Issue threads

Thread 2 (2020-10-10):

Where can I see the demo video？

cgrrty, 2020-10-10:
Where can I see the demo video

Ezward, 2020-12-29:
I currently do not have a video of the rover in action.  My current prototype works well, but is very ugly; I'd like to do a second build that looks better before I post a video.  I was hoping to get autonomous path following working before I made the project really public, but I may do that sooner.  At this point (tag v0.7) I have pretty good speed control and pose estimation working.  I also have telemetry being plotted in realtime.  So I think I need to do at least two videos at first; 1) How to build the rover 2) How to calibrate and operate it using the web ui.

cgrrty, 2021-02-02:
Hi
I am a hardware engineer. I want to join in and design pcb for this project
thanks

Ezward, 2021-02-05:
Hi @cgrrty That is exciting.  I've added a slapdash wiring diagram to the documentation; you can look at that.  I'll also post a few pictures of the prototype; it's a lot of cardboard and tape so I've avoided posting photos, but they are probably worth posting if you want to see how this thing works.  This weekend I will also post a short video of the go-to-goal behavior in action.  You will see in the photos that the ESP32 cam is mounted up on a 'stand' currently made of cardboard and foamboard.  If you are going to design a PCB for this, it would be really cool to have a board that also serves as the 'stalk' for the camera; so a long-ish PCB that could be stood on it's end so the camera is up high.  We could design a 3d printed base that the PCB could be inserted into to hold it at a good angle for the camera to see in front of it.

cgrrty, 2021-02-07:
Hi Ezward
Can you publish videos on bilibili ([](https://www.bilibili.com/))at the same time? I think more people will see and be interested in this way

Ezward, 2021-02-14:
@cgrrty I've added video links to the documentation.  So for there are 3 videos;

EzRover Introduction, https://youtu.be/yN2ya2mlBNU
EzRover Calibration, https://youtu.be/ciDCUUx8MXI
EzRover Go to Goal Behavior, https://youtu.be/_eKCqswX5D0

I'll look at getting these up on bilibili.

There is also a slideshow (under construction) that describes the algorithms used in EzRover; https://docs.google.com/presentation/d/1t77gDPORG4qcxwhPNWrPlTVjwQWncRw7ujsnF02ZN7E/edit?usp=sharing

Future videos will be on
- Gamepad connection and control
- A video showing the rover in operation
- discussion of C++ internals and extension points
- discussion of JavaScript internals and extension points

Ezward, 2021-02-15:
@cgrrty Here is a video showing the robot in action; https://youtu.be/TjE9ceNOTJE

cgrrty, 2021-02-15:
Very good video, if posted on bilibili, more people will watch it.
I'm sure they'll be interested, too.
Very good video, if posted on bilibili, more people will watch it. I'm sure they'll be interested, too.
If the language is a problem for you, I can post it on your behalf.

cgrrty, 2021-02-15:
Science and technology video like this
[https://www.bilibili.com/video/BV1UE411P7hx?from=search&seid=16049779974724068010]()

Ezward, 2021-02-16:
I could probably figure out how to sign up and post a video on bilibili using google translate, but I could not provide a good description.  I doubt google will do a good job translating.

cgrrty, 2021-02-17:
Hi
I will upload the video to bilibili sometime, which may take some time.
There is no problem with the overview you wrote in Chinese.
Later, I will buy materials to build the prototype first.
After that, I will design the schematic first, and then I will draw the PCB after you review it.
By the way, what software do you usually use to design PCB and schematics on your side?

Ezward, 2021-02-17:
@cgrrty I'm a software guy; I've not designed a PCB before.  So something open source that would run on Linux; maybe KiCad.  I can provide input on physical form factor that would work well for the robot.  I also have a number of ideas about how to improve the robot's hardware.  Some of those are discussed in the docs.  Specifically, I want to create a version of the robot that use a PCA9685 module to control the motors; that will free up some pins.  With those pins we can re-enable serial port or we can support quadrature encoder motors.  So we would connect to the PCA9685 over I2C, the use it to drive the motor's PWM duty cycle.  We could then also add other I2C devices to that bus, like an OLED display.  I don't think we need to put the PCA9685 functionality on the board, we just need to make sure the I2C pins on the ESP32Cam are available so we can add an external module.

Closed 2023-05-15.

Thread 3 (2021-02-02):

How to compile the code correctly？

cgrrty, 2021-02-02:
HI
I has been able to successfully compile the code，But the serial port does not output debug information
How to set up to print the following statement like ` "Setting up..." ...Wifi initialized, running on IP Address: `
```
//
// Include _after_ encoder stuff so SERIAL_DISABLE is correctly set
//
// leave LOG_LEVEL undefined to turn off all logging
// or define as one of ERROR_LEVEL, WARNING_LEVEL, INFO_LEVEL, DEBUG_LEVEL
//
#define LOG_LEVEL DEBUG_LEVEL
#include "log.h"
```
```
void setup()
{
    //
    // initialize serial monitor
    // NOTE: if SERIAL_DISABLE is defined, then SERIAL_xxxx calls are all no-ops
    //
    SERIAL_BEGIN(115200);
    SERIAL_DEBUG(true);
    SERIAL_PRINTLN();

    LOG_INFO("Setting up...");

    //
    // init wifi
    //
    WiFi.mode(WIFI_STA);
    WiFi.begin(ssid, password);
    if (WiFi.waitForConnectResult() != WL_CONNECTED)
    {
        LOG_ERROR("WiFi Failed!\n");
        return;
    }

    SERIAL_PRINT("...Wifi initialized, running on IP Address: ");
    SERIAL_PRINTLN(WiFi.localIP().toString());
    SERIAL_PRINT("ESP Board MAC Address:  ");
    SERIAL_PRINTLN(WiFi.macAddress());
```

```
[env]
src_build_flags =
	-D SERIAL_DISABLE=0
	-D USE_WHEEL_ENCODERS=0
	-D USE_ENCODER_INTERRUPTS=0
    -include arduino.h

[env:esp32cam]
platform = espressif32
board = esp32cam
framework = arduino
monitor_speed = 115200
lib_deps =
	ESP Async WebServer
	WebSockets
```

Ezward, 2021-02-02:
That definitely needs some documentation.  The underlying issue here is that the ESP32Cam has very few available GPIO pins, so the output of the wheel encoder LM393 Optocoupler modules use the TX/TR pins, which means no serial.  However, if you want serial, you can change the compile options in the platformio.ini file.  This is what it looks like by default:
`src_build_flags =
	-D SERIAL_DISABLE=1
	-D USE_WHEEL_ENCODERS=1
	-D USE_ENCODER_INTERRUPTS=1
    -include arduino.h
`
So you can remove `-D USE_WHEEL_ENCODERS=1` and `-D SERIAL_DISABLE=1`, then the serial output will work, but encoders will not (and so speed control, pose estimation and go to goal behavior will not work correctly).

A future hardware configuration will include a PCA9685 board which talks I2C; we can use that to generate the PWM for the motors and so free up a net of 2 pins, which we could then use for the encoder inputs.  I wanted to start with the minimum possible hardware config/cost to see how far we could get with it.

Ezward, 2021-02-02:
I just pushed a little document update to that effect.  I will add a circuit diagram tonight so you can see how the camera, motor driver and optocouplers are connected.  Thank you for building the code; please feel free to file issues such as this one; it will help the code base a lot.

Ezward, 2021-02-02:
To be extra clear, you want to delete the `-D SERIAL_DISABLE=1` and `-D USE_WHEEL_ENCODERS=1` entries, not just set them to zero.  The checks to see of those symbols are defined, so defining them a zero still leaves them as defined.

cgrrty, 2021-02-03:
I remove -D USE_WHEEL_ENCODERS=1 and -D SERIAL_DISABLE=1
Compilation failed
```
[env]
src_build_flags =
	; -D SERIAL_DISABLE=1
	; -D USE_WHEEL_ENCODERS=1
	-D USE_ENCODER_INTERRUPTS=1
    -include arduino.h

[env:esp32cam]
platform = espressif32
board = esp32cam
framework = arduino
monitor_speed = 115200
lib_deps =
	ESP Async WebServer
	WebSockets

```

```
Compiling .pio\build\esp32cam\src\parse\parse_numbers.cpp.o
Compiling .pio\build\esp32cam\src\parse\parse_strings.cpp.o
src\main.cpp: In function 'void setup()':
src\main.cpp:223:13: error: 'leftWheelEncoderPtr' was not declared in this scope
             leftWheelEncoderPtr,
             ^
src\main.cpp:228:13: error: 'rightWheelEncoderPtr' was not declared in this scope
             rightWheelEncoderPtr,
             ^
Compiling .pio\build\esp32cam\src\rover\goto_goal.cpp.o
Compiling .pio\build\esp32cam\src\rover\pose.cpp.o
*** [.pio\build\esp32cam\src\main.cpp.o] Error 1
================================================== [FAILED] Took 22.97 seconds ==================================================
```

cgrrty, 2021-02-03:
I modified the code in two places and the code was compiled successfully
```
#ifdef USE_WHEEL_ENCODERS
    Encoder leftWheelEncoder(LEFT_ENCODER_PIN, 0);
    Encoder *leftWheelEncoderPtr = &leftWheelEncoder;
#else
    Encoder *leftWheelEncoderPtr = NULL;
#endif
```
```
#ifdef USE_WHEEL_ENCODERS
    Encoder rightWheelEncoder(RIGHT_ENCODER_PIN, 1);
    Encoder *rightWheelEncoderPtr = &rightWheelEncoder;
#else
    Encoder *rightWheelEncoderPtr = NULL;
#endif
```
```
--- Available filters and text transformations: colorize, debug, default, direct, hexlify, log2file, nocontrol, printable, send_on_enter, time
--- More details at http://bit.ly/pio-monitor-filters
--- Miniterm on COM3  115200,8,N,1 ---
--- Quit: Ctrl+C | Menu: Ctrl+T | Help: Ctrl+T followed by Ctrl+H ---

INFO: Setting up...
```
But there are still problems with serial output.
The serial port only outputs a sentence and then stops
`INFO: Setting up...`
But the device shows that it is connected to the hotspot of my phone，I think the devive is working,just serial output is wrong.
I don't know why

Ezward, 2021-02-03:
Line 54 of main.cpp defines the logging level
```
#define LOG_LEVEL INFO_LEVEL
```
Try setting that to `DEBUG_LEVEL`

I will check in a change to fix that compile error.

Ezward, 2021-02-03:
Note I also made a bug fix the log.h, so you should get the latest code.

cgrrty, 2021-02-03:
The serial port output is normal
The esp32 development board I used does not have a camera
Later I will change to a development board with a camera to test

```
--- Available filters and text transformations: colorize, debug, default, direct, esp32_exception_decoder, hexlify, log2file, nocontrol, prntable, send_on_enter, time
--- More details at http://bit.ly/pio-monitor-filters
--- Miniterm on COM5  115200,8,N,1 ---
--- Quit: Ctrl+C | Menu: Ctrl+T | Help: Ctrl+T followed by Ctrl+H ---

INFO: Setting up...
...Wifi initialized, running on IP Address: 192.168.43.48
ESP Board MAC Address:  24:6F:28:AF:4A:7C
INFO: ... http server intialized ...
INFO: ... websockets server intialized ...
[E][camera.c:1249] esp_camera_init(): Camera probe failed with error 0x20001
ERROR: Camera init failed with error 0x
ERROR: 131073
INFO: ...Rover Initialized...
INFO: handling /
INFO: handling /bundle.css
INFO: handling /bundle.js
INFO: handling /status
Guru Meditation Error: Core  1 panic'ed (LoadProhibited). Exception was unhandled.
Core 1 register dump:
PC      : 0x400d1a4b  PS      : 0x00060c30  A0      : 0x800d24f1  A1      : 0x3ffd4870
A2      : 0x3ffd4894  A3      : 0x3ffc1b41  A4      : 0x3ffc1b40  A5      : 0x00000000
A6      : 0x00ff0000  A7      : 0xff000000  A8      : 0x800d1a31  A9      : 0x3ffd4850
A10     : 0x00000000  A11     : 0x400e5818  A12     : 0x00000008  A13     : 0x00000010
A14     : 0x3ffd6878  A15     : 0xff000000  SAR     : 0x00000018  EXCCAUSE: 0x0000001c
EXCVADDR: 0x0000000c  LBEG    : 0x400014fd  LEND    : 0x4000150d  LCOUNT  : 0xffffffff

Backtrace: 0x400d1a4b:0x3ffd4870 0x400d24ee:0x3ffd4890 0x40182a43:0x3ffd48e0 0x400dbe35:0x3ffd4900 0x400d9dd1:0x3ffd4940 0x400d9e9f:0x3ffd480 0x400da125:0x3ffd49c0 0x40170295:0x3ffd49e0 0x40170311:0x3ffd4a20 0x40170a4e:0x3ffd4a40 0x4008dbe1:0x3ffd4a70

Rebooting...
ets Jun  8 2016 00:22:57

rst:0xc (SW_CPU_RESET),boot:0x13 (SPI_FAST_FLASH_BOOT)
configsip: 0, SPIWP:0xee
clk_drv:0x00,q_drv:0x00,d_drv:0x00,cs0_drv:0x00,hd_drv:0x00,wp_drv:0x00
mode:DIO, clock div:2
load:0x3fff0018,len:4
load:0x3fff001c,len:1044
load:0x40078000,len:8896
load:0x40080400,len:5828
entry 0x400806ac

INFO: Setting up...
ERROR: WiFi Failed!

INFO: Setting up...
...Wifi initialized, running on IP Address: 192.168.43.48
ESP Board MAC Address:  24:6F:28:AF:4A:7C
INFO: ... http server intialized ...
INFO: ... websockets server intialized ...
[E][camera.c:1249] esp_camera_init(): Camera probe failed with error 0x20001
ERROR: Camera init failed with error 0x
ERROR: 131073
INFO: ...Rover Initialized...

INFO: Setting up...
ERROR: WiFi Failed!

ets Jun  8 2016 00:22:57

rst:0x1 (POWERON_RESET),boot:0x13 (SPI_FAST_FLASH_BOOT)
configsip: 0, SPIWP:0xee
clk_drv:0x00,q_drv:0x00,d_drv:0x00,cs0_drv:0x00,hd_drv:0x00,wp_drv:0x00
mode:DIO, clock div:2
load:0x3fff0018,len:4
load:0x3fff001c,len:1044
load:0x40078000,len:8896
load:0x40080400,len:5828
entry 0x400806ac

INFO: Setting up...
ERROR: WiFi Failed!

ets Jun  8 2016 00:22:57

rst:0x1 (POWERON_RESET),boot:0x13 (SPI_FAST_FLASH_BOOT)
configsip: 0, SPIWP:0xee
clk_drv:0x00,q_drv:0x00,d_drv:0x00,cs0_drv:0x00,hd_drv:0x00,wp_drv:0x00
mode:DIO, clock div:2
load:0x3fff0018,len:4
load:0x3fff001c,len:1044
load:0x40078000,len:8896
load:0x40080400,len:5828
entry 0x400806ac

INFO: Setting up...
...Wifi initialized, running on IP Address: 192.168.43.48
ESP Board MAC Address:  24:6F:28:AF:4A:7C
INFO: ... http server intialized ...
INFO: ... websockets server intialized ...
[E][camera.c:1249] esp_camera_init(): Camera probe failed with error 0x20001 0x20001
ERROR: Camera init failed with error 0x
ERROR: 131073
INFO: ...Rover Initialized...
INFO: handling /
INFO: handling /bundle.css
INFO: handling /bundle.js
INFO: handling /status
Guru Meditation Error: Core  1 panic'ed (LoadProhibited). Exception
was unhandled.
Core 1 register dump:
PC      : 0x400d1a4b  PS      : 0x00060a30  A0      : 0x800d24f1  A1      : 0x3ffd48d0
A2      : 0x3ffd48f4  A3      : 0x3ffc1b41  A4      : 0x3ffc1b40  A5      : 0x00000000
A6      : 0x00ff0000  A7      : 0xff000000  A8      : 0x800d1a31  A9      : 0x3ffd48b0
A10     : 0x00000000  A11     : 0x400e5818  A12     : 0x00000008  A13     : 0x00000010
A14     : 0x3ffd5bd4  A15     : 0xff000000  SAR     : 0x00000018  EXCCAUSE: 0x0000001c
EXCVADDR: 0x0000000c  LBEG    : 0x400014fd  LEND    : 0x4000150d  LCOUNT  : 0xffffffff

Backtrace: 0x400d1a4b:0x3ffd48d0 0x400d24ee:0x3ffd48f0 0x40182a43:0x3ffd4940 0x400dbe35:0x3ffd4960 0x400d9dd1:0x3ffd49a0 0x400d9e9f:0x3ffd49e0 0x400da125:0x3ffd4a20 0x40170295:0x3ffd4a40 0x40170311:0x3ffd4a80 0x40170a4e:0x3ffd4aa0 0x4008dbe1:0x3ffd4ad0

Rebooting...
ets Jun  8 2016 00:22:57

rst:0xc (SW_CPU_RESET),boot:0x13 (SPI_FAST_FLASH_BOOT)
configsip: 0, SPIWP:0xee
clk_drv:0x00,q_drv:0x00,d_drv:0x00,cs0_drv:0x00,hd_drv:0x00,wp_drv:0x00
mode:DIO, clock div:2
load:0x3fff0018,len:4
load:0x3fff001c,len:1044
load:0x40078000,len:8896
load:0x40080400,len:5828
entry 0x400806ac

INFO: Setting up...
ERROR: WiFi Failed!

INFO: Setting up...
...Wifi initialized, running on IP Address: 192.168.43.48
ESP Board MAC Address:  24:6F:28:AF:4A:7C
INFO: ... http server intialized ...
INFO: ... websockets server intialized ...
[E][camera.c:1249] esp_camera_init(): Camera probe failed with error 0x20001
ERROR: Camera init failed with error 0x
ERROR: 131073
INFO: ...Rover Initialized...
INFO: handling /
INFO: handling /bundle.css
INFO: handling /bundle.js
INFO: handling /status
Guru Meditation Error: Core  1 panic'ed (LoadProhibited). Exception
was unhandled.
Core 1 register dump:
PC      : 0x400d1a4b  PS      : 0x00060430  A0      : 0x800d24f1  A1      : 0x3ffd4850
A2      : 0x3ffd4874  A3      : 0x3ffc1b41  A4      : 0x3ffc1b40  A5      : 0x00000000
A6      : 0x00ff0000  A7      : 0xff000000  A8      : 0x800d1a31  A9      : 0x3ffd4830
A10     : 0x00000000  A11     : 0x400e5818  A12     : 0x00000008  A13     : 0x00000010
A14     : 0x3ffd5a4c  A15     : 0xff000000  SAR     : 0x00000018  EXCCAUSE: 0x0000001c
EXCVADDR: 0x0000000c  LBEG    : 0x400014fd  LEND    : 0x4000150d  LCOUNT  : 0xffffffff

Backtrace: 0x400d1a4b:0x3ffd4850 0x400d24ee:0x3ffd4870 0x40182a43:0x3ffd48c0 0x400dbe35:0x3ffd48e0 0x400d9dd1:0x3ffd4920 0x400d9e9f:0x3ffd4960 0x400da125:0x3ffd49a0 0x40170295:0x3ffd49c0 0x40170311:0x3ffd4a00 0x40170a4e:0x3ffd4a20 0x4008dbe1:0x3ffd4a50

Rebooting...

INFO: Setting up...
ERROR: WiFi Failed!

```
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

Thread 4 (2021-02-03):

Make camera support optional

Ezward, 2021-02-03:
The code can be downloaded onto a normal ESP32 board, but it will crash when it attempts to initialize the camera.  It would be a nice feature to be able to build without camera support so the basic rover can run on an ESP32.
- Add a preprocessor flag ENABLE_ESP32_CAMERA that must be defined for the Esp32Cam camera code to be included in the compile.
- Add and endpoint to check for camera support; if camera is supported this returns true, false otherwise
- Have the web client check the endpoint at startup and hide or show the camera controls based on the return value.  Default should be to hide the camera support.

Ezward, 2021-02-04:
I did part one of this; the c++ code now uses the preprocessor symbol ENABLE_CAMERA to enable camera support.  It is defined in platformio.ini by default, so camera is enabled by default.  Remove that line from platformio.ini and you should be able to download to a normal ESP32.  You may want to pick a different board type in platformio.ini rather than esp32cam.

Note that if you are using a regular ESP32, you will probably have enough pins to support both the wheel encoders and the serial port.  You may need a minor code change to make that work; I believe there are one or two places that will define `SERIAL_DISABLE` if `USE_WHEEL_ENCODERS` is defined; you would want to make those two symbols orthogonal.

This commit only addresses the C++ code.  The Web camera UI will still be present, but non-functional.  A later commit will hide the camera ui if the camera is not enabled.

Ezward, 2021-02-07:
@cgrrty When you get a chance, please pull the latest code and let me know if this fix works on the esp32.  I found a bug in the esp32cam if we turn off the camera; the encoder interrupts to not work.  This can be compensated for if we also undefine `USE_ENCODER_INTERRUPTS`, then the encoder pins will be polled and this makes speed control and pose estimation continue to work.  I don't think that will be necessary on a normal esp32; please let me know when you get a chance.  Then I can close this bug.

Ezward, 2021-02-14:
@cgrrty Have you been able to build and run the code on an ESP32 yet?

cgrrty, 2021-02-14:
Hi  Ezward
After trying, the compilation can be passed, and it can be run.
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

Ezward, 2021-02-16:
Closing as done.  Thanks.

Closed 2021-02-16.

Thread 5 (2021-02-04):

About network issues

cgrrty, 2021-02-04:
Hi
I have two questions，about wireless networks
1、Whether the device can use a fixed ip to quickly link the device？
2、Can automatically reconnect after network failure？
Thanks

Ezward, 2021-02-04:
1. Current code simply connects to the wifi indicated in wifi_credentials.h.  You can use your wifi router's admin to choose an ip for the rover.  This is often called IP Address Reservation in that admin ui.  I could add a mode where the rover servers as an access point; then the computer of phone would connect to it.  If that sounds like what you are asking, let me know (or add a feature request in issues!).
2. The rover will try to reconnect after a failure, but I have found it to be unreliable.  There is some work to do there.  I probably need to do a more thorough reload of the client, as if the page was reloaded.

cgrrty, 2021-02-04:
HI
   The rover can be set as an access point but it is not necessary.
Setting the rover  as  an access point will cause the mobile phone or computer  cannot be accessed Internet  normally when they are connect to the  rover’s network,
thanks

cgrrty, 2021-02-04:
HI
   The rover can be set as an access point but it is not necessary.
Setting the rover  as  an access point will cause the mobile phone or computer  cannot be accessed Internet  normally when they are connect to the  rover’s network,
thanks

Ezward, 2021-02-05:
Did this answer your question?

Closed 2021-02-08.

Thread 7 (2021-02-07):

Speed control is broken on Esp32Cam if ENABLE_CAMERA is not defined

Ezward, 2021-02-07:
There was a previous commit that create a new preprocessor symbol, `ENABLE_CAMERA`, that must be defined for the camera support to be fully compiled into the rover's C++ code.  By default this is defined in platformio.ini.
When it is not defined, the camera api is turned into function that just return failure, exception for `getCameraPropertiesJson()` which is the method underlying the `status/` endpoint.  When camera is enabled, it return all the camera properties and an `enabled` property with value of "true".  When camera is disabled, it only returns `enabled` with value of "false".
So that's the context.  The bug is that if ENABLE_CAMERA is not defined, then speed control does NOT work.  The issue seems to be the interrupts are not firing, so the encoder never counts any ticks.  This is likely because the camera internals may turn on interrupts, but if we don't initialize it, they never get turned on.
- One way to confirm this is to disable the camera AND encoder interrupts;  to do this, comment out these two lines in platformio.ini;
```
    -D USE_ENCODER_INTERRUPTS=1
    -D ENABLE_CAMERA=1
```
- This will then make the rover C++ code using polling to read the encoder; this is not very accurate, but if it works it would prove the issue is with interrupts.
- If it is interrupts, then we probably have to make a call to enable interrupts ourselves.

Ezward, 2021-02-07:
I did the experiment where I disabled the camera and used polling for the encoder ticks, but the bug was the same.  So rather than and interrupt issue, it seems to be an issue where the input pins for the encoder pins are not working; we are not seeing any edges as we should see.
- One more thing to think about; we are re-using the serial TX/RX pins for the encoder input pins; I'm very sure the camera code was using the serial port as it starts up; so it may make sure the pins are working as part of it's code.
- So now we can focus on how to make those pins active input pins when the camera is turned off.

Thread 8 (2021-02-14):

I did measure the latency

cgrrty, 2021-02-14:
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
Can we learn something from this project? [https://github.com/OpenHD/Open.HD/wiki](url)

cgrrty, 2021-02-14:
The picture is instantaneous, and sometimes the  latency is more serious.

Ezward, 2021-02-15:
I'll take a look.

Ezward, 2021-02-15:
They mention a best case latency of 40 to 50ms, which is pretty good.   It looks like what they are doing is using low level access to the wifi chips in some usb wifi adapters to create a lower latency protocol.

Ezward, 2021-02-16:
I'm going to close this issue and we can track the other two issues that came out of this.  Thanks.

Closed 2021-02-16.

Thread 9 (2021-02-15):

Implement bluetooth gamepad connection between Esp32Cam and PS3 controller.

Ezward, 2021-02-15:
**Why**
As discussed in [issue #8](https://github.com/Ezward/Esp32CameraRover2/issues/8#issuecomment-778923255), we would like to reduce the input latency between the rover and the gamepad.  Currently we are using a gamepad attached to the web application's browser, so it incurs the latency across the websocket connection.  Further, we (in another issue) would like to implement a peer-to-peer FPV video solution, so attaching a gamepad to the browser would not make sense.

**What**
Implement bluetooth gamepad connection between Esp32Cam and PS3 controller.  See these:
- https://github.com/jvpernis/esp32-ps3
- https://techtutorialsx.com/2020/02/16/esp32-connecting-a-ps3-controller/

We will need to turn the returned values into wheel speed (tank style) inputs from 0 to 1.0.  We do this in the javascript code now.  This involves a mapping of gamepad axis to command inputs.  We should put this into config in a header file; they can be fairly static because we intend to use us a PS3 joystick for now.  However, we do want these in constants so we could change them if we implement another gamepad.

See these javascript files for current gamepad implementation.
- https://github.com/Ezward/Esp32CameraRover2/blob/master/client/js/gamepad.js
- https://github.com/Ezward/Esp32CameraRover2/blob/master/client/js/rover_command.js
- https://github.com/Ezward/Esp32CameraRover2/blob/master/client/js/rover_view_manager.js

cgrrty, 2021-02-18:
Hi
Can both modes be supported（Retain the previous mode）， Let users choose.
For users who require low latency,  can use the PS3 controller
For users who require low latency,  can use the web application controller
I don't know if it will have any impact on the program.

Ezward, 2021-02-18:
Yes, we will make it so the user can choose.  I think I will add a panel to the Rover Control section that will facilitate pairing with a bluetooth gamepad.  So it will be just one more input type.

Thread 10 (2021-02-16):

Prototype EspNow peer to peer video

Ezward, 2021-02-16:
**Why**
As discussed in [issue #8](https://github.com/Ezward/Esp32CameraRover2/issues/8), we would like to reduce the video latency between the rover and the gamepad in order to make FPV mode more usable.  One potential latency is the protocol between the rover and the web application.  The [Open.HD](https://github.com/OpenHD/Open.HD) project has addressed this issue in part by writing code to create a custom peer to peer connection between RaspberryPi endpoints using usb wifi adapters' radios.  Espressif had created a similar peer to peer protocol between Esp32 endpoints called EspNow.

**What**
Implement a peer to peer video protocol from an Esp32Cam to an Esp32 with a TFT display using EspNow.  Measure the latency of transmitting a frame from the Esp32Cam to the endpoint.  Compare the peer to peer latency with the web app's websocket latency.

Ezward, 2021-02-17:
EspNow will not work for video; it has a a maximum message length of just 250 bytes.  So let's keep the **Why** part of this ticket, but change the **What**.  I'm going to close this issue.

I've created a new [issue](https://github.com/Ezward/Esp32CameraRover2/issues/11) to try a different approach

First, let's measure the latency in our current setup where the Esp32Cam in configured as a station and then connects to some local access point.  So in this setup, the client also connects to that access point and can then load the web application using the rover's ip address.  So the web socket packets must pass through the access point in this configuration.

Then let's implement a scheme where we make the Esp32Cam an access point and connect directly to that access point to load the web application.  That scheme eliminates the router as the middle man.  This may also simply connecting to the rover if we can choose it's ip address on the network; then we can know a priori what that is; no messing with router ip-allocation.  Once we implement that scheme, then measure the latency; hopefully eliminating the router will speed things up.

cgrrty, 2021-02-18:
The analysis process is useful.

Closed 2021-02-17.

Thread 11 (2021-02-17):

Implement rover as access point and compare latency

Ezward, 2021-02-17:
**Why**
As discussed in [issue #8](https://github.com/Ezward/Esp32CameraRover2/issues/8), we would like to reduce the video latency between the rover and the gamepad in order to make FPV mode more usable.  One potential latency is the protocol between the rover and the web application.  The [Open.HD](https://github.com/OpenHD/Open.HD) project has addressed this issue in part by writing code to create a custom peer to peer connection between RaspberryPi endpoints using usb wifi adapters' radios.  Espressif had created a similar peer to peer protocol between Esp32 endpoints called EspNow.  However, EspNow is not suitable for transferring video because it limits a message to 250 bytes.  Instead, we would like to see if removing the router from our current setup reduces latency.

Our current wifi setup configures the rover's Esp32Cam as a wifi station that connects to a wifi access point.  The client also connects to that wifi access point, then uses the Esp32Cam's ip address to load the web application.  This presents two issues; first we have to know that ip address that the router assigned to the Esp32Cam.  Second and more importantly to this ticket, websocket packets must transit the wifi router to get from rover to client browser.  We want to see if removing that wifi router from the middle can reduce latency.  As a potential side benefit, it may simplify connecting to the rover.

**What**
Implement a wifi configuration where the rover's Esp32Cam is configured as an access point.  The device that will run the web browser will then connect directly to that access point.  This will eliminate the intervening wifi router.  Note we may need to implement a wifi configuration where the rover's Esp32Cam is both an access point and a station, so that it can serve the web application, serve the camera status endpoints and join the websocket connection.

Once this configuration is working, measure the video latency between the rover and the web client.

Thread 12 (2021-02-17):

Design integrated PCB that can run the framework

Ezward, 2021-02-17:
Let's start to collect requirements here
- on board ESP32Cam functionality (Esp32 + camera)
- on board motor driver and power circuitry
- we can discuss power handling.  I am currently using a 5v USB power bank.  This works well to deliver 5v to Esp32Cam and also delivers power to motors.   However, motors are rated at a higher power and would work a little better with 6v.  Setting up power is one of the biggest pains for beginners, so that is why I chose the USB power bank.  So we should keep simplicity in mind.
- make sure I2S bus pins are exposes so we can add I2S modules like PCA9685 or OLED display.
- form factor should make it easy to mount as a front-facing camera.  This is one of the biggest pains with the ESP32Cam; it has no mounting holes and it is hard to get to the reset button.  We should try to address those issues in this design.

Ezward, 2021-02-17:
Expressif has announced the Esp32-S3 dual core LX7 microcontroller.  This is a little faster and has some SIMD instructions to speed up machine learning algorithms.  It's probably very close in pins to the Esp32-S2, but it had dropped CAN-bus for instance.  It also adds USB support directly to the chip (No external programmer needed!)

Ezward, 2021-02-17:
I'm not using the SD card functionality on the ESP32Cam currently.  I'd probably rather have those pins freed up that have the SD card.  But you may disagree.  What might we do with it?  I could see a function where we could tell the rover to record to the SD card when it finds something interesting.  For instance, we could use a neural network running on the web application to recognize cats and dogs, then send a command to the rover to take a picture.   That would be fun.  What do you think?

cgrrty, 2021-02-18:
Hi
   I want to design a bottom board
- One power module, power supply for all modules
- ESP32Cam can be plugged into it. （Or some other type of core board.）
- Some fixed holes will be left on the bottom board to fix the motor that drives the wheel.
- Motor speed measuring module （Mybe two IO）
- Motor drive module（PCA9685 ）
-SD can be retained on the core board
ps
 Esp32-S3, I'll get to know it when I have time.

cgrrty, 2021-02-18:
The first version of PCB may be more like a test board. （Will gradually improve）
It is mainly used for preliminary verification of the scheme.

cgrrty, 2021-02-18:
Pcb is produced very quickly on our side.
I'm not used to debugging hardware with hole boards right now, so I want to design a version of PCB.
My English is not very good.
If I have grammatical or lexical problems, you can point out.

Ezward, 2021-02-18:
I understand; you would like to create a PCB that acts as the chassis to the rover as well as the circuitry.  That is very cool.  I like that idea.

We definitely need a wheel encoder on each wheel of the two wheels; that is necessary for speed control.

You English is infinitely better than my attempts at your language!

Ezward, 2021-02-18:
Doing a little 'competitive analysis' I know there are a number of robots build using the microbit board that use a PCB-as-chassis design.

They often use a smaller (and higher quality) N20 gear motor.  This one uses N20 motors with hall-effect quadrature encoders: https://www.amazon.com/DFROBOT-Maqueen-Micro-Programming-Educational/dp/B089CS3NXJ/ref=asc_df_B07Y37Q3WK/. That is a very nice configuration that would provide more precise speed control that the cheaper gear motors and optical encoders that I'm currently using.  They also cost a bit more.  This is kit is about $55USD before shipping.

Here is one that uses yellow gear motors; note it does not have encoders; we would want allow for encoders; https://chicagodist.com/products/kitronik-move-motor-for-the-bbc-micro-bit
But this is much cheaper ($30USD) than the above kit.  It still look very compact.

The microbit brain is about $15USD, but does not include a camera.  I think the Esp32Cam is cheaper, has a true wifi chip and a camera, so it could provide a more capable robot for less money.

cgrrty, 2021-02-19:
Hi
I found two car chassis.They're all cheap.
Their quality may not be very good.
I want to choose some good accessories and remake them.
Which is more suitable for us, four-wheel drive or two-wheel drive?
There is a rotational speed measurement on each wheel.
The price is between $2USD and $8USD.
Here are the links. I don't know if the links are valid for you？
https://item.taobao.com/item.htm?spm=a230r.1.14.14.4e054795bivS8u&id=522578524873&ns=1&abbucket=1#detail
https://item.taobao.com/item.htm?spm=a230r.1.14.35.4e054795bivS8u&id=538177034577&ns=1&abbucket=1#detail

cgrrty, 2021-02-19:
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

Ezward, 2021-02-19:
I have been using the two wheel drive chassis that that you have pictured.  I have not tried the 4 wheel drive model.  We are already running short of pins on the ESP32cam, so we would not have enough pins to read the wheel encoders for the 4 wheel drive version.

Ezward, 2021-03-03:
check out the 3d printed camera mount in https://github.com/Ezward/Esp32CameraRover2/blob/master/docs/building_the_rover.md; it will mount on either of the chassis you linked to.

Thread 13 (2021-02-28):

Discussion on the Standard of remote Control Protocol

cgrrty, 2021-02-28:
Hi
I see an esp32 project, which realizes the control of drone. The protocol of the remote control part is standard. Can we use it for reference?
https://michalschwarz.github.io/rc-controller/esp32/quadcopter/f450/asgard32/schema/2019/05/07/esp32-drone-v1.0.0.html

cgrrty, 2021-02-28:
Are you trying to compile this project?
I compiled it successfully, but unfortunately, when the phone is connected to AP, esp32 will restart.
I don't know what the problem is. It would be great if you could help me.
Looking forward to your reply!

Ezward, 2021-03-03:
esp32 restart generally means it is not getting enough power.  The esp32cam pull a lot of power when it first starts.  Also, any issues with common ground between motors and esp32 (and the serial adapter for programming) can cause a reboot.  I would try these;

- Reboots may happen if you have the serial programmer connected when you reboot; I always disconnect it before restarting the esp32cam.
- disconnect power from motors (don't send power to L9110S) and try booting; if it boots then it's possible you don't have enough power for both the motors and ESP32.  Note that in my setup, once and while when I boot after programming the esp32 the app will not start correctly; if I then just reboot using the reset button it will start; I suspect cold-boot draws too much current as both the esp32 and motor driver are starting from off.  So when I reset, both esp32 and motor driver are already powered up and so there is not as much of a current draw so it succeeds.
- The application is not designed for more than one client to connect at one time.  So if you have a phone and a desktop web browser connected, it may cause the app to crash.  That being said, I have definitely connected using the web browser on my phone and successfully drove the rover.

Can you tell me now you have your rover powered?  Can you send a photo?  Thanks.

Ezward, 2021-03-03:
As for the protocol between the rover and the web client I agree we could improve this.  I wanted a text protocol so it is easy to debug.  Also, I wanted to be able to acknowledge receipt of a command.  The protocol has two features that work together for this purpose; 1) each command is given an id from a monotonically incrementing id, which also allows commands to be ordered on the other end, 2) command receipt is acknowledged by reflecting the received command back to the client, but in an 'ack' package.

I'm happy to look at improving the protocol by implementing something more standard.  I'll take a look at what you linked.

Ezward, 2021-03-03:
I did a little research on that link you provided.  That project is using the IBUS serial protocol to talk between an Arduino and an RC receiver.  The IBUS protocol seems to be dedicated to this application; you send send/receive servo values and sensor values.  It is not a general serial protocol that would support our application.  For instance, there is no way to send a 'goto' command to the rover using that protocol.

Ezward, 2021-11-10:
The gopigo robot uses an custom HAT that includes a microcontroller.  It interfaces to the host RaspberryPi using the I2C bus and a binary protocol.  See [gopig github](https://github.com/DexterInd/GoPiGo/tree/master/Firmware)  This has a lot of functions going on in it.

Openbot uses an Arduino for low level control of motors, LEDs and for reading encoders.  It uses serial (via USB) to talke to an Android phone.  Here is the [OpenBot firmware](https://github.com/isl-org/OpenBot/blob/master/firmware/openbot_v1_nano/openbot_v1_nano.ino).  It's very low level and does not actually do speed control or pose estimation.

I like an ascii human readable protocol because you can test the robot via the serial port without the need for a controlling computer.  It also makes debug output easy and obvious.  So what we have so far is pretty good; we should look at abstracting how commands are sent and responses and telemetry received so we can make the bot work with serial port (and so make the code run on an OpenBot) or via I2C (so it we can make it run on a Gopigo)

Ezward, 2023-05-22:
I think we can do better by:

- message number: I was calling this command id or command number.  This is the monotonically increasing id produced by the sender of the message.  It provides uniqueness and ordering.  So the rover itself will generate a new message number for each message it sends through the web socket to the web UI.  The web ui will generate a new message number for each command/message it sends to the rover via the web socket.  The message number is unique for a given web socket.  If a client has more than one websocket it does not need to try to keep the message number's unique across all websockets; however when acknowledging a message it must send the acknowledgment on the same web socket that it received it on so that the original message id makes sense to the receiver of the acknowledgment.

1. Make sure each message is 100% json, so rather than `set({"left":{"forward":true,"pwm":217}})` it would be `{"set":{"left":{"forward":true,"pwm":217}}}`.  That makes it much easier to parse a command and dispatch it.
2. move towards using schemas to reduce the size of packets, so `{"forward":true,"pwm":217}` would have a schema that defines the field names, their types and their ordering so that we could send `[true,217]` and still reliable validate and decode it.  It remains valid json, but it requires the schema to re-hydrate it to `{"forward":true,"pwm":217}`.  So effectively a struct format for the data.  So the full command message might be `["set", ["left", [true,217]]]` if it was fully schema'd.  Or possibly even `["set","left",true,217]` to set a single value or `["set",[["left",true,217],["right",true,195]]` if the command allows for multiple values to be set with a single command. We could reduce this further if we assigned numerical enum values for "set" and "left".  Further we could use 0 and 1 for boolean values rather than `false` and `true`.  That being said, using strings does make this easier to read for a person and does not give up that much in space relative to a 32bit number.
3. We still want a container that includes the monotonically increasing message number and the checksum/CRC and we would like that to also be json, so something like `[12345, ["set", ["left", [true,217]]], 3254]` where the first number is the monotonically increasing message number, the second field is the command and its arguments and the third field is the checksum, which is the command number plus checksum of the command computed from the command rendered as a string.  So if the message was actually an empty string (so it' checksum is zero) then the checksum would equal the message number.
4. Acknowledgements can be very short, `[13427, ["ack", 12345], 213]`, where first field is the response message number, second field is "ack"  and third field is CRC of "ack" plus the command number.

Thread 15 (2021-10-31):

Redesign Encoder polling code

Ezward, 2021-10-31:
Rewrite the encoder polling code to act like the mono encoder sketch I create for the DonkeyCar project.  See https://github.com/autorope/donkeycar/tree/921-next-generation-odometer-parts/arduino

The mono encoder does a reasonable job of reading encoder pulses while debouncing, all without interrupts.

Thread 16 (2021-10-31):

Support 'forward only' motor control mode

Ezward, 2021-10-31:
Currently each wheel uses two pwm pins, one for forward and one for backward.  This is good because it (a) allows us to backup (b) allows us to turn in place.  However, if we only support a forward pwm pin on each motor, then we would have two free pins.  This would then allow us to read the encoders with those pins.  Then we could support use of the serial ports without having to disconnect that encoders.
- support compile-time optional drive train mode where we only supply forward pwm to each wheel.
- when the firmware is compiled in this mode, the Turtle Control web UI must hide the 'Reverse' button because the rover cannot drive in reverse.
- when the firmware is compiled in forward-only mode the Go to goal must use a slightly different 'Turn to Angle' algorithm.
- when the firmware is compiled in forward-only mode, the Game Controller support in the web UI must use a slightly different algorithm that does not allow for reverse.  Perhaps simply setting any reverse value to zero is adequate.
- when the firmware is compiled in forward-only mode, allow the serial port to be activated even if encoders are activated.  The encoder pins will be reassigned to the former reverse pwm pins in this mode.

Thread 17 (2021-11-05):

Implement autonomous mode using Tensorflow.js

Ezward, 2021-11-05:
See this repo for an example using the Udacity Self Driving Simulator; https://github.com/bakoushin/self-driving-car-javascript

Here is a medium article about this; https://levelup.gitconnected.com/run-a-self-driving-car-using-javascript-and-tensorflow-js-8b9b3f7af23d

### Strategy:
- This is mediated by the webUI.  The user interacts with the web ui in 3 modes; collection mode, training mode and autopilot mode.
- The client can save some complete models locally (in indexDB), so it can run those models even if the server is not running.
- Normal telemetry displayed in collection mode and autopilot mode.
- Training actually happens in a server (probably nodejs) application.  During training the rover can continue to be operated, including running collection or autopilot mode.

### Collection Mode
- The user chooses collection mode and provides the address of the server and chooses to start a new data set or append to the current data set.
- The webui closes it's camera socket
- The webui opens a socket to the server
- The webui sends the address of the rover to the server
- The rover opens a camera socket to the rover
- When the user selects to start capture or capture is triggered automatically by a non-zero throttle, the webui sends a message to the server to start recording.
- The server chooses the data set or creates a new one depending on what the webui indicated.
- We will modify the camera socket so that the rover always sends metadata with the image; steering angle, throttle, angular velocity, linear velocity, pose.x, pose.y, pose.angle, timestamp
- The server will save the data as it arrives (naming each image uniquely and in a way that is increasing monotonically, probably saving the metadata in a csv file and including relative path to the image)
- The server will forward the data to the webui through it's websocket so it can be displayed.
- When the web ui indicates recording should stop, the server stops saving data to the dataset and closes it's websocket connection to the rover.  The webui reopens it's camera socket connection to the rover.

### Training Mode
- The user chooses training mode and provides the address of the server (we will remember this in localstorage so we can provide a good default).
- The webui connects to the server (if it is not already) and asks for the list of datasets.
- The webui shows the list of datasets.
- The user checks the datasets they wish to train on.
- The webui sends a message to the server with the list of datasets to train on.
- The server starts training and sends status updates to the webui.
- The webui shows the status of the training.
- When completed, the server saves the model to disk and messages the webui, the webui saves the model in indexedDb

### Autopilot Mode
- The user chooses autopilot mode and optionally prov
- The webui shows the models that are saved in indexedDb
- If connected to a server, the webui asks for the list of models persisted to disk and merges this with those saved locally in indexedDB
- The user chooses a model.
- The pose is reset to (0, 0, 0)
- The webui enters the autopilot loop;
  - an image and metadata are received from the rover.
  - using the image, a steering angle is inferred using the model.
  - the steering angle and throttle are sent to the rover.
  - the rover uses an inverse kinematic model to calculate wheel velocities to match the desires velocity and steering angle and updates the wheel velocities.  All normal telemetry is sent to the client and the client displays the telemetry.
- The user chooses to stop autopilot in the webui
  - The webui tells the rover to stop
  - The webui exits the autopilot loop

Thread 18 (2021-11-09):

Improve camera frame rate

Ezward, 2021-11-09:
Camera frame rate is influences by
- image size; smaller images, especially 640x480 and below, produce better frame rates
- number of frame buffers allocated.  There should be at least 2 buffers allocated.  This is only possible for lower resolution modes and with PRAM available.
- The clock rate.  It turns out a lower clock rate can enhance framerate on low resolutions, perhaps because all the work the sensor does can be done within a single frame.  See https://github.com/espressif/esp32-camera/issues/15

Tasks;
- experiment with combinations of image size, frame buffers and clock rate to optimize frame rate
  - do this with and without factoring in the transfer of the images, so that we see the raw rate and the overhead imparted by transferring to the web UI.
- Add a compile flag to fix the frame size, number of buffers allocated and the clock rate to the chose parameters
-  Hide the camera properties UI when the image properties are fixed.
- Hard code the camera properties endpoint to return the fixed properties.

Donkeycar uses 160x120, so that might be what we want here.  However 640x480 is much better quality for FPV, so maybe we want a way to switch between these two mode.

thet0ast3r, 2022-02-02:
Hi, @Ezward , did you manage to find something about increasing the framerate? Im using arduino ide, and struggle with the driver. Greetings.

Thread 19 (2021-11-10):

See if we can implement OTA updates

Ezward, 2021-11-10:
If we can set up our partition so it can handle both the camera output, see [Issue 18](https://github.com/Ezward/Esp32CameraRover2/issues/18) and OTA, then we can use OTA during development to push new code.  This would then allow forward/revers of both wheels and use of the encoders because we would not need to download via the serial rx/tx pins; we could do it with an ota.

This ticket is for a discussion and to capture relevant research.

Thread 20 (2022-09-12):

Support L293DD

samuk, 2022-09-12:
Hi I'm working on a ESP32 open hardware bot: https://github.com/rosmo-robot/micro-bot/tree/master/Hardware/V2.11

Would your code support this hardware?

samuk, 2022-09-12:
I guess the biggest change would be hall encoders?

samuk, 2022-09-13:
Hall encoders need 2x pins each, so I don't think ESPcam has sufficient pins?

https://github.com/rosmo-robot/micro-bot/blob/master/Hardware/V2.11/Minisumo_V2.1.pdf

samuk, 2022-09-15:
Maybe with https://www.aliexpress.com/item/1005004360195123.html

Ezward, 2023-05-01:
Sorry I have not responded, I've been focused on Donkeycar.  I'm back on this project.  Yes I have one of the new Esp32 cams as well and they have more pins.

With the older cam we can still use the hall encoder but we would only use one channel per wheel.  Alternatively we could change the bot so that it could not reverse - that gives use two pins to use which could be used for the second encoder channel on each wheel; however that doesn't really get use much because if we can't go in reverse then we don't need the encoder to be able to detect this and so a single channel encoder is fine.

Ezward, 2023-05-01:
We can support the L293D with the current code I think because the L9119 and the L293D both use two PWM pins per motor to handle forward and reverse.

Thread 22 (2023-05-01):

Implement basic authentication for the rover's web ui and web socket api

Ezward, 2023-05-01:
Currently any one can control the robot if they have or can guess its IP address.  We want to add optional basic authentication such that the user can configure username and password that is compiled into the firmware and is used for basic authentication.  If either the username or the password is empty then no authentication is done.  If both the username and password are not empty then they are used as the credentials for the web ui and web socket api as follows:
- The use is challenged for a username and password using the browser's default basic authentication dialog when the user opens the web ui.
- The web server checks the `Authorization` header for the web ui GET and the web socket GET as follows;
  - If the `Authorization` header is missing then the request fails with a 401 Not Authorized response
  - If the `Authorization` header exists but does not match the configured username and password then the request fails with a 403 Forbidden response.
  - If valid of the `Authorization` header matches the configured username and password then the requests succeed.

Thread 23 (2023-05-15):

Save calibration values in browser

Ezward, 2023-05-15:
We currently have to re-input our motor and speed control calibration values each time the rover is started.  It would be better to save these in the browser and reload them when the application is started.

- When we save calibration values to the rover, also save them in the browser.

This has a forward looking benefit; if we implement a simulator in the browser then it will also have access to saved calibration values.

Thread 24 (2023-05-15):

Save calibration values on rover

Ezward, 2023-05-15:
The esp32cam has the ability to write to SD card and to local flash memory.  We should save calibration values that are sent to the rover in flash.  We then also have to tell the web application what these values are when it asks, so we need an api for this.

- save calibration values to flash when the web application sends them to the rover.
- implement a web-socket api for asking for the calibration values.  Design this so that the response may be used as a push value (at some point the rover may push these values over the web socket rather than waiting to be asked for them).

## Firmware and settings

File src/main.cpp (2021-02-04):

// #include <Arduino.h>
#ifdef ESP32
#include <AsyncTCP.h>
#include <WiFi.h>
#elif defined(ESP8266)
#include <ESP8266WiFi.h>
#include <ESPAsyncTCP.h>
#endif
#include <ESPAsyncWebServer.h>
#include <WebSocketsServer.h>

#include "config.h"

// gzipped html content
#include "camera/camera_index.h"
#include "camera/camera_wrap.h"
#include "websockets/stream_socket.h"

#include "string/strcopy.h"
#include "websockets/command_socket.h"
#include "serial.h"
#include "gpio/pwm.h"
#include "motor/motor_l9110s.h"
#include "encoder/encoder.h"
#include "wheel/drive_wheel.h"
#include "telemetry.h"

//
// control pins for the L9110S motor controller
//
#include "rover/rover.h"
#include "rover/goto_goal.h"
#include "rover/rover_command.h"

//
// wheel encoders use same pins as the serial port,
// so if we are using encoders, we must disable serial output/input
//
#ifdef USE_WHEEL_ENCODERS
    #ifdef SERIAL_DISABLE
        #undef SERIAL_DISABLE
    #endif
    #define SERIAL_DISABLE  // disable serial if we are using encodes; they use same pins
#endif

bool builtInLedOn = false;

//
// Include _after_ encoder stuff so SERIAL_DISABLE is correctly set
//
// leave LOG_LEVEL undefined to turn off all logging
// or define as one of ERROR_LEVEL, WARNING_LEVEL, INFO_LEVEL, DEBUG_LEVEL
//
#define LOG_LEVEL INFO_LEVEL
#include "log.h"

//
// put ssid and password in wifi_credentials.h
// and do NOT check that into source control.
//
#include "wifi_credentials.h"
//const char* ssid = "******";
//const char* password = "******";

//
// camera web service endpoints
//
void statusHandler(AsyncWebServerRequest *request);
void configHandler(AsyncWebServerRequest *request);
void captureHandler(AsyncWebServerRequest *request);

// health endpoint
void healthHandler(AsyncWebServerRequest *request);

// 404 not found handler
void notFound(AsyncWebServerRequest *request);

//
// Create all the parts for the rover.
// It's CRITICAL that PwmChannels exist for life of the motor instance
//

MessageBus messageBus;
TelemetrySender telemetry;

// left drive wheel
PwmChannel leftForwardPwm(A1_A_PIN, LEFT_FORWARD_CHANNEL, MotorL9110s::pwmBits());
PwmChannel leftReversePwm(A1_B_PIN, LEFT_REVERSE_CHANNEL, MotorL9110s::pwmBits());
MotorL9110s leftMotor;
#ifdef USE_WHEEL_ENCODERS
    Encoder leftWheelEncoder(LEFT_ENCODER_PIN, 0);
    Encoder *leftWheelEncoderPtr = &leftWheelEncoder;
#else
    Encoder *leftWheelEncoderPtr = NULL;
#endif
DriveWheel leftWheel(LEFT_WHEEL_SPEC, WHEEL_CIRCUMFERENCE);

// right drive wheel
PwmChannel rightForwardPwm(B1_B_PIN, RIGHT_FORWARD_CHANNEL, MotorL9110s::pwmBits());
PwmChannel rightReversePwm(B1_A_PIN, RIGHT_REVERSE_CHANNEL, MotorL9110s::pwmBits());
MotorL9110s rightMotor;
#ifdef USE_WHEEL_ENCODERS
    Encoder rightWheelEncoder(RIGHT_ENCODER_PIN, 1);
    Encoder *rightWheelEncoderPtr = &rightWheelEncoder;
#else
    Encoder *rightWheelEncoderPtr = NULL;
#endif
DriveWheel rightWheel(RIGHT_WHEEL_SPEC, WHEEL_CIRCUMFERENCE);

// rover
TwoWheelRover rover(WHEELBASE);
RoverCommandProcessor roverCommandProcessor;

// rover behaviors
GotoGoalBehavior gotoGoalBehavior;

// create the http server
AsyncWebServer server(80);

/**
 * Arduino setup
 * - called once by Arduino framework before loop() 
 *   so that systems can be initialized.
 */
void setup()
{
    //
    // initialize serial monitor
    // NOTE: if SERIAL_DISABLE is defined, then SERIAL_xxxx calls are all no-ops
    //
    SERIAL_BEGIN(115200);
    SERIAL_DEBUG(true);
    SERIAL_PRINTLN();

    LOG_INFO("Setting up...");

    // 
    // init wifi
    //
    WiFi.mode(WIFI_STA);
    WiFi.begin(ssid, password);
    if (WiFi.waitForConnectResult() != WL_CONNECTED)
    {
        LOG_ERROR("WiFi Failed!\n");
        return;
    }

    SERIAL_PRINT("...Wifi initialized, running on IP Address: ");
    SERIAL_PRINTLN(WiFi.localIP().toString());
    SERIAL_PRINT("ESP Board MAC Address:  ");
    SERIAL_PRINTLN(WiFi.macAddress());

    //
    // init web server
    //

    // endpoints to return the compressed html/css/javascript for the browser web application
    server.on("/", HTTP_GET, [](AsyncWebServerRequest *request) {
        LOG_INFO("handling " + request->url());
        AsyncWebServerResponse *response = request->beginResponse_P(200, "text/html", index_html_gz, sizeof(index_html_gz));
        response->addHeader("Content-Encoding", "gzip");
        request->send(response);
    });
    server.on("/bundle.css", HTTP_GET, [](AsyncWebServerRequest *request) {
        LOG_INFO("handling " + request->url());
        AsyncWebServerResponse *response = request->beginResponse_P(200, "text/css", bundle_css_gz, sizeof(bundle_css_gz));
        response->addHeader("Content-Encoding", "gzip");
        request->send(response);
    });
    server.on("/bundle.js", HTTP_GET, [](AsyncWebServerRequest *request) {
        LOG_INFO("handling " + request->url());
        AsyncWebServerResponse *response = request->beginResponse_P(200, "text/javascript", bundle_js_gz, sizeof(bundle_js_gz));
        response->addHeader("Content-Encoding", "gzip");
        request->send(response);
    });

    // endpoint to check server health
    server.on("/health", HTTP_GET, healthHandler);

    // endpoint for streaming video from camera
    server.on("/control", HTTP_GET, configHandler);     // set a single camera setting
    server.on("/status", HTTP_GET, statusHandler);      // return camera settings
    server.on("/capture", HTTP_GET, captureHandler);    // return a single image
    server.on("/stream", HTTP_GET, notFound /*videoHandler*/);  // we've decprecated and moved into websockets

    // return 404 for unhandled urls
    server.onNotFound(notFound);

    // start the server listening for requests
    server.begin();
    LOG_INFO("... http server intialized ...");

    //
    // initialize websockets for streaming video and rover commands
    //
    wsStreamInit();
    wsCommandInit();
    LOG_INFO("... websockets server intialized ...");

    //
    // create background task to execute queued rover tasks
    //
    // xTaskCreate(roverTask, "roverTask", 1024, NULL, 1, &roverTaskHandle);

    //
    // initialize the camera
    //
    initCamera();

    //
    // initialize rover dependancies
    //
    // NOTE: This MUST happen AFTER other initializations.
    //       I suspect that the camera or wifi code uses the 
    //       serial pins when they first start, however we use the 
    //       serial port pins for the wheel encoders.  So we must 
    //       attach to those pins after those systems are started.
    //
    telemetry.attach(&messageBus);
    rover.attach(
        leftWheel.attach(
            leftMotor.attach(leftForwardPwm, leftReversePwm), 
            leftWheelEncoderPtr, 
            PULSES_PER_REVOLUTION, 
            &messageBus),
        rightWheel.attach(
            rightMotor.attach(rightForwardPwm, rightReversePwm), 
            rightWheelEncoderPtr, 
            PULSES_PER_REVOLUTION, 
            &messageBus),
        &messageBus);
    gotoGoalBehavior.attach(rover, messageBus).startListening();
    roverCommandProcessor.attach(rover, gotoGoalBehavior);

    #ifdef USE_WHEEL_ENCODERS
        // internal led will blink on each wheel rotation
        pinMode(BUILTIN_LED_PIN, OUTPUT);
    #endif

    LOG_INFO("...Rover Initialized...");

}

/**
 * Arduino main loop
 * - called after setup() 
 * - called continuously by Arduino framework as fast as possible.
 */
void loop()
{
    // poll all rover systems (motor, encoders, speed controllers)
    rover.poll(millis());
    roverCommandProcessor.pollRoverCommand(millis());
    telemetry.poll();   // send any buffered telemetry

    // poll stream to send image to clients via websocket
    #ifdef ENABLE_CAMERA
        wsStreamCameraImage();
    #endif
    wsStreamPoll();

    // poll stream that gets command via websocket
    wsCommandPoll();

    #ifdef USE_WHEEL_ENCODERS
        //
        // blink built-in led on each wheel revolution
        //
        const unsigned int leftWheelCount = rover.readLeftWheelTicks();
        const boolean ledOn = (0 == (leftWheelCount / (PULSES_PER_REVOLUTION / 2)) % 2);
        if (ledOn != builtInLedOn) {
            digitalWrite(BUILTIN_LED_PIN, ledOn ? LOW : HIGH);  // built in led uses inverted logic; low to light
            builtInLedOn = ledOn;
        }
    #endif
}


/************ web server endpoint handlers ************/
// These are called by the webserver when a request 
// for the associated url is received.
// They should not be called directly.

/**
 * Handle request for unknown url with a 404 response code
 */
void notFound(AsyncWebServerRequest *request)
{
    request->send(404, "text/plain", "Not found");
}


/**
 * Health endpoint returns 200 with json body
 * indicating health of server
 */
void healthHandler(AsyncWebServerRequest *request)
{
    LOG_INFO("handling " + request->url());

    // TODO: determine if camera and rover are healty
    request->send(200, "application/json", "{\"health\": \"ok\"}");
}

/**
 * handle /capture endpoints
 * - return 200 response with a single jpeg camera image 
 * - on error, return 500 with text body indicating the error
 */
void captureHandler(AsyncWebServerRequest *request)
{
    LOG_INFO("handling " + request->url());

    //
    // 1. create buffer to hold image
    // 2. capture a camera image
    // 3. create response and send it
    // 4. free the image buffer
    //
 
 
    // 1. create buffer to hold frames
    uint8_t* jpgBuff = new uint8_t[68123];  // TODO: should be based on image dimensions
    size_t   jpgLength = 0;

    // 2. capture a camera image
    esp_err_t result = grabImage(jpgLength, jpgBuff);

    // 3. create and send response
    if(result == ESP_OK){
        request->send_P(200, "image/jpeg", jpgBuff, jpgLength);
    }
    else
    {
        request->send(500, "text/plain", "Error capturing image from camera");
    }

    //
    // 4. free the image buffer
    //
    delete jpgBuff;
}


/**
 * Handle /status web service endpoint;
 * - return all the camera configuration settings
 * - response body is is json payload with
 *   all camera properties and values like;
 *   `{"framesize":0,"quality":10,"brightness":0,...,"special_effect":0}`
 */
void statusHandler(AsyncWebServerRequest *request) 
{
    LOG_INFO("handling " + request->url());

    const String json = getCameraPropertiesJson();
    request->send_P(200, "application/json", (uint8_t *)json.c_str(), json.length());
}


/**
 * Set a single camera configuration parameter using the /control endpoint
 * - uses a GET requests with two query parameters that both must be present
 *   - 'var' is the name of the configuration variable
 *   - 'val' is the value of the configuration variable to set
 */
void configHandler(AsyncWebServerRequest *request) {
    LOG_INFO("handling " + request->url());

    //
    // validate parameters
    //
    String varParam = "";
    if (request->hasParam("var", false))
    {
        varParam = request->getParam("var", false)->value();
    }
    
    String valParam = "";
    if (request->hasParam("val", false))
    {
        valParam = request->getParam("val", false)->value();
    }

    // we must have values for each parameter
    if (varParam.isEmpty() || valParam.isEmpty()) 
    {
        request->send(400, "text/plain", "bad request; both the var and val params must be present.");
    }
    else
    {
        const int status = setCameraProperty(varParam, valParam);
        if(SUCCESS != status) {
            LOG_ERROR("Failure setting camera property");
        }
        request->send((SUCCESS == status) ? 200: 500);
    }
}

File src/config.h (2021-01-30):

#ifndef CONFIG_H
#define CONFIG_H

#include "./util/math.h"

typedef float distance_type;    // from pose.h
typedef float speed_type;       // from drive_wheel.h
typedef long encoder_count_type;// from encoder.h

//
// constants used to configure the application at compile time
//

// pin assignments for motor controller
const int A1_A_PIN = 15;    // left forward input pin
const int A1_B_PIN = 13;    // left reverse input pin
const int B1_B_PIN = 14;    // right forward input pin
const int B1_A_PIN = 2;     // right reverse input pin

const int LEFT_FORWARD_CHANNEL = 12;    // pwm write channel
const int LEFT_REVERSE_CHANNEL = 13;    // pwm write channel
const int RIGHT_FORWARD_CHANNEL = 14;   // pwm write channel
const int RIGHT_REVERSE_CHANNEL = 15;   // pwm write channel


// wheel encoder config
const int LEFT_ENCODER_PIN = 3;             // left LM393 wheel encoder input pin
const int RIGHT_ENCODER_PIN = 1;            // right LM393 wheel encoder input pin
const int PULSES_PER_REVOLUTION = 20 * 2;   // number of slots in encoder wheel * 2 (for changing edge)

const int BUILTIN_LED_PIN = 33;    // not the 'flash' led, the small led

// speed controller constants
const unsigned int CONTROL_POLL_MS = 20;        // how often to run speed controller
const unsigned int CONTROL_HISTORY_LENGTH = 2;  // number of samples used for smoothing speed control
const unsigned int CONTROL_HISTORY_MS = CONTROL_POLL_MS * CONTROL_HISTORY_LENGTH;   // time interval for smoothing speed control
const speed_type SPEED_TOLERANCE = 0.3;         // +/- range for target speed
const encoder_count_type CONTROL_MIN_ENCODER_COUNT = PULSES_PER_REVOLUTION / 4;     // travel at least 1/4 turn before calculating velocity
const unsigned int CONTROL_SETTLE_MS = 20;     // number of milliseconds after changing direction that we
                                               // we continue to integrate encoder ticks in the prior direction
                                               // in order to handle inertia.
// pose
const unsigned int POSE_POLL_MS = 20;        // how often to run pose estimation
const encoder_count_type POSE_MIN_ENCODER_COUNT = CONTROL_MIN_ENCODER_COUNT;     // travel at least 1/5 turn before updating pose


// const float WHEEL_CIRCUMFERENCE = 1.0;  // distance is revolutions, speed is revolutions/sec
// const float WHEEL_CIRCUMFERENCE = PULSES_PER_REVOLUTION;  // distance is pulses, speed is pulses/sec
const float WHEEL_DIAMETER_CM = 6.97;   // centimeters
const float WHEEL_CIRCUMFERENCE = WHEEL_DIAMETER_CM * PI;  // distance is cm, speed is cm/sec
const distance_type WHEELBASE = 13.5;   // centimeters

const distance_type POINT_FORWARD_FRACTION = 0.75;  // position of forward control point as fraction of wheelbase

#endif // CONFIG_H

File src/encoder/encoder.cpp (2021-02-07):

// #include <Arduino.h>
#include "encoder.h"

#define LOG_LEVEL DEBUG_LEVEL
#include "./log.h"

// defined in encoderInterrupts.cpp
extern bool encoderInterruptAttached(encoder_iss_type interruptServiceSlot);
extern bool attachEncoderInterrupt(Encoder &encoder, encoder_iss_type interruptServiceSlot);
extern bool detachEncoderInterrupt(Encoder &encoder, encoder_iss_type interruptServiceSlot);


/**
 * Get gpio input pin, passed to constructor
 */
gpio_type Encoder::pin() // RET: gpio input pin for encoder
{
    return this->_pin;
}


/**
 * Get the current encoder count.
 * This is a signed value that may increase or decrease
 * depending on the direction the wheel is turning.
 */
encoder_count_type Encoder::count() // RET: current encoder count
{
    ++this->_readingCount;  // set semaphore
    const encoder_count_type c = this->_count;    // read the value
    --this->_readingCount;  // reset semaphone
    return c;               // return the value
}

/**
 * Get the current encoder ticks.
 * This is an unsigned value that always increases,
 * counting ticks independent of wheel direction.
 */
encoder_count_type Encoder::ticks() // RET: current encoder ticks
{
    ++this->_readingCount;  // set semaphore
    const encoder_count_type c = this->_ticks;    // read the value
    --this->_readingCount;  // reset semaphone
    return c;               // return the value
}

/**
 * Set the direction in which the encoder will increment.
 * Optical encoders cannot encode direction natively,
 * but the motor control logic knows, so it can tell
 * the encoder using this method.
 * A quadrature encoder can encode direction, so 
 * it would call setDirection() prior to calling encode()
 * 
 * Set the number of milliseconds the encoder will
 * continue to integrate ticks in the prior direction.
 * This handles inertia associated with stopping or
 * abrupt changes in direction.
 */
void Encoder::setDirection(
    encoder_direction_type direction)   // IN : encoder_forward, encoder_stopped, encoder_reverse
{
    //
    // if we are transitioning from a forward or reverse direction
    // then we want to make sure we integrate using the prior direction
    // for a short time to handle inertia.
    //
    // If we are transitioning from stopped, then integrate 
    // in the new direction.
    //
    ++this->_settingDirection;    // so ISR knows not to use this state while it is changing
    this->_settleDirection = this->_direction ? this->_direction : direction;  // remember inertial direction
    this->_settleTimeMs = millis() + this->_settleMs;
    this->_direction = direction;
    --this->_settingDirection;    // now safe for ISR to use this state
}

/**
 * Get the current encoder direction
 */
encoder_direction_type Encoder::direction()    // RET: encoder_forward, encoder_stopped, encoder_reverse
{
    return this->_direction;
}

/**
 * Increment the encoder based on the direction.
 * When using an interrupt service routine, it
 * should call this method.
 */
void FASTCODE Encoder::encode()  
{
    //
    // direction config includes several properties
    // including a 4-byte time value.  We don't want
    // to be reading these while the outer code
    // is part-way through changing them.  So we look
    // at the one-byte semaphore, which can be written
    // atomically by the outer code; if it is non-zero
    // then it indicates the outer code has started
    // setting these properties and so this ISR
    // cannot reliably use those values.  Instead
    // we default to the current direction. If the semaphore
    // is zero then we can safely read the properties
    // and use them to compute the direction.
    //
    const encoder_direction_type direction = 
        (this->_settingDirection || (millis() > this->_settleTimeMs)) 
        ? _direction 
        : _settleDirection;

    //
    // This method is called by an external
    // interrupt service routine, so it is
    // possible for it to interrupt reading
    // of the 4 byte count.  To avoid reading
    // a partially committed value, we keep a 
    // second, buffered count which we can increment
    // at will.  We add this to the readable
    // count only if it is not currently being read.
    // This avoids turning off/on interrupts during
    // the read, which is expensive.  
    //
    this->_bufferedCount += (encoder_count_type)direction;
    this->_bufferedTicks += 1;
    if(!this->_readingCount) {                  // if semaphore is not set
        this->_count += this->_bufferedCount;   // write the value
        this->_bufferedCount = 0;               // clear the buffered value
        this->_ticks += this->_bufferedTicks;
        this->_bufferedTicks = 0;
    }
} 

/**
 * Determine if encoder is attached to pin
 */
bool Encoder::attached()     // RET: true if attached, false if not
{
    return this->_attached;
}


/**
 * Set the pin mode and enable polling
 */
void Encoder::attach() {
    pinMode(_pin, INPUT_PULLUP);
    if(this->_interrupt_slot >= 0) {
        attachEncoderInterrupt(*this, this->_interrupt_slot);
    }
    _attached = true;
}

/**
 * Disable polling
 */
void Encoder::detach() {
    if(this->_interrupt_slot >= 0) {
        detachEncoderInterrupt(*this, this->_interrupt_slot);
    }
    _attached = false;
}

/**
 * Read the pin state
 */
gpio_state Encoder::readPin() // RET: pin state GPIO_LOW or GPIO_HIGH
{
    if(attached()) {
        return (gpio_state)digitalRead(_pin);
    }
    return GPIO_LOW;
}

/**
 * Poll the gpio pin to watch for RISING transition.
 * 
 * NOTE: This method exists for the case where an external
 *       interrupt service routine cannot be used to watch
 *       the input pin.  In that case, polling is the only option.
 * 
 * NOTE: You must call attach() before you start calling poll().
 *       You must call poll at least twice as fast an you believe
 *       transitions will happen in order to get an accurate count.
 *       For instance, if it is an optical wheel encoder with 10 slots,
 *       then there will be 10 RISING transitions and 10 FALLING
 *       transitions with each rotation of the encoder/wheel.
 *       If the wheels maximum RPM is expected to be 100 RPM, then
 *       minimum poll() = (100 / 60) * 20 * 2 ~= 67 per second.
 */      
void Encoder::poll() {
    if(_attached) {
        //
        // only do this if not using interrupts
        //
        #ifndef USE_ENCODER_INTERRUPTS
            // we encode on any transition edge
            gpio_state newState = readPin();
            if(newState != _pinState) {
                _pinState = newState;
                encode();
            }
        #endif
    }
}

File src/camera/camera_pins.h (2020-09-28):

#ifndef CAMERA_CAMERA_PINS_H
#define CAMERA_CAMERA_PINS_H

#if defined(CAMERA_MODEL_WROVER_KIT)
#define PWDN_GPIO_NUM    -1
#define RESET_GPIO_NUM   -1
#define XCLK_GPIO_NUM    21
#define SIOD_GPIO_NUM    26
#define SIOC_GPIO_NUM    27

#define Y9_GPIO_NUM      35
#define Y8_GPIO_NUM      34
#define Y7_GPIO_NUM      39
#define Y6_GPIO_NUM      36
#define Y5_GPIO_NUM      19
#define Y4_GPIO_NUM      18
#define Y3_GPIO_NUM       5
#define Y2_GPIO_NUM       4
#define VSYNC_GPIO_NUM   25
#define HREF_GPIO_NUM    23
#define PCLK_GPIO_NUM    22

#elif defined(CAMERA_MODEL_ESP_EYE)
#define PWDN_GPIO_NUM    -1
#define RESET_GPIO_NUM   -1
#define XCLK_GPIO_NUM    4
#define SIOD_GPIO_NUM    18
#define SIOC_GPIO_NUM    23

#define Y9_GPIO_NUM      36
#define Y8_GPIO_NUM      37
#define Y7_GPIO_NUM      38
#define Y6_GPIO_NUM      39
#define Y5_GPIO_NUM      35
#define Y4_GPIO_NUM      14
#define Y3_GPIO_NUM      13
#define Y2_GPIO_NUM      34
#define VSYNC_GPIO_NUM   5
#define HREF_GPIO_NUM    27
#define PCLK_GPIO_NUM    25

#elif defined(CAMERA_MODEL_M5STACK_PSRAM)
#define PWDN_GPIO_NUM     -1
#define RESET_GPIO_NUM    15
#define XCLK_GPIO_NUM     27
#define SIOD_GPIO_NUM     25
#define SIOC_GPIO_NUM     23

#define Y9_GPIO_NUM       19
#define Y8_GPIO_NUM       36
#define Y7_GPIO_NUM       18
#define Y6_GPIO_NUM       39
#define Y5_GPIO_NUM        5
#define Y4_GPIO_NUM       34
#define Y3_GPIO_NUM       35
#define Y2_GPIO_NUM       32
#define VSYNC_GPIO_NUM    22
#define HREF_GPIO_NUM     26
#define PCLK_GPIO_NUM     21

#elif defined(CAMERA_MODEL_M5STACK_WIDE)
#define PWDN_GPIO_NUM     -1
#define RESET_GPIO_NUM    15
#define XCLK_GPIO_NUM     27
#define SIOD_GPIO_NUM     22
#define SIOC_GPIO_NUM     23

#define Y9_GPIO_NUM       19
#define Y8_GPIO_NUM       36
#define Y7_GPIO_NUM       18
#define Y6_GPIO_NUM       39
#define Y5_GPIO_NUM        5
#define Y4_GPIO_NUM       34
#define Y3_GPIO_NUM       35
#define Y2_GPIO_NUM       32
#define VSYNC_GPIO_NUM    25
#define HREF_GPIO_NUM     26
#define PCLK_GPIO_NUM     21

#elif defined(CAMERA_MODEL_AI_THINKER)
#define PWDN_GPIO_NUM     32
#define RESET_GPIO_NUM    -1
#define XCLK_GPIO_NUM      0
#define SIOD_GPIO_NUM     26
#define SIOC_GPIO_NUM     27

#define Y9_GPIO_NUM       35
#define Y8_GPIO_NUM       34
#define Y7_GPIO_NUM       39
#define Y6_GPIO_NUM       36
#define Y5_GPIO_NUM       21
#define Y4_GPIO_NUM       19
#define Y3_GPIO_NUM       18
#define Y2_GPIO_NUM        5
#define VSYNC_GPIO_NUM    25
#define HREF_GPIO_NUM     23
#define PCLK_GPIO_NUM     22

#else
#error "Camera model not selected"
#endif

#endif // CAMERA_CAMERA_PINS_H

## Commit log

2020-06-13 Esp32CameraRover2 - switch to PlatformIO
2020-06-14 Esp32CameraRover2 - now request handle queues the command and returns to client and a FreeRTOS task executes commands in the queue in the background.
2020-06-14 Esp32CameraRover2 - minor comment formatting
2020-06-19 v0.3 - added /image /status /control endpoints by porting ESP32CameraWebServer code
2020-06-20 v0.3.1 - fixed bug in executeRoverCommand; was using global speed rather that speedParam
    [rover_l9110s.cpp]
2020-06-20 v0.3.2 added minor code so we can ask for currently executing command
2020-06-21 v0.3.0 -now client opens socket to start streaming and closes it to stop streaming.
2020-06-21 v0.4.0 -client opens socket to start streaming, closes it to stop streaming
2020-06-22 v0.4.0 - Fixed crash above 640x480 resolution
    [camera_wrap.cpp, main.cpp]
2020-06-22 v0.4.1 -added html buttons for controlling rover from phone
2020-06-23 v0.4.0 -added buttons to web UI to control rover
2020-07-04 -updated direction button styles -added modified analog write polyfill library -started description of UI in README.md
2020-07-13 -changed GamePadViewController to lookup elements at start; -fixed some bugs associated with renaming throttle/steering to axisOne/axisTwo
2020-07-20 -added MessageBus and TurtleViewManager to handle switching control modes. Still a work in progress; need to add code for more than Turtle mode
2020-08-01 -updated tests to use 'String' type, like Arduino code
2020-08-03 -fixed issue with switch tabs and losing joystick control
    [main.cpp]
2020-08-05 -fixed bug parseCommand() -added code to ack/nack a command -made client wait for ack() before sending next command so we don't overload the websocket server
    [main.cpp, rover.h, rover_l9110s.cpp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]
2020-08-09 -updated gamepad UI to include zero area and flip checkbox -update tank command code to utilize zero area, flipping and a motor stall value -all of this makes control with joystick much better
2020-08-09 -added motor view controller to edit motor stall values -updated TankCommand to use stall values when commanding tank
    [main.cpp]
2020-08-21 -increased command rate -added more loop processing for command socket -all of this to make commands more responsive
2020-09-12 -refactored to allow either encoders OR serial io
2020-09-20 -refactor to move things out of main and into their own modules -big fix for interupt routine issues requires ESP32 specific code
    [camera_wrap.cpp, main.cpp]
2020-09-20 -made engine stall slider 100 steps -added comment for encodes -saved changes to platformio.ini to disable serial and enable encoders
2020-09-28 -refactoed rover into layered, dependant classes; rover, motor, encoder, pwm, gpio
2020-09-28 -moved websockets into their own folder -hooked up interupt service routine for new encoder implementation
2020-10-03 -refactor try to get interrupts to work, but they still do NOT work. Polling mode works.
    [encoder.cpp, main.cpp, rover.cpp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]
2020-10-03 - moved initialization of rover, encoders and interrupts after wifi and camera. That fixes the interrupts issue. At this point, the rover is counting wheel encoder using interrupts.
    [main.cpp, rover.cpp]
2020-10-10 -refactored encoders.cpp to be in the encoder module; much cleaner implementation now
2020-10-10 -abstracted out the drive wheels into their own class. That is the level at which we will used closed-loop pid control for speed
2020-10-11 -added PID speed controller, but have not tested it yet.
2020-10-12 -small tweak of PID to assume always positivie pwm output values
2020-10-20 -changed history queue implementation and refactored a little to eliminate a couple of bugs. -removed unnecessary messages.
    [config.h, drive_wheel.cpp, drive_wheel.h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]
2020-10-21 Created CircularBuffer class to clean up history in wheel's control code.
2020-10-25 -have constant speed controller working -pid does NOT work yet -need to send stall values so we can avoid windup
    [drive_wheel.cpp, drive_wheel.h, main.cpp]
2020-10-26 - fixed bug in command queue processing that could freeze the rover
    [config.h, drive_wheel.cpp, drive_wheel.h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]
2020-11-02 - removed the plugable speed controllers until I can get them to work correctly. - client now sends 0 to 1.0 for stall value; modified stall command to use this. - added a log() message to telemetry,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
    [config.h, drive_wheel.cpp, drive_wheel.h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]
2020-11-03 -configured encoder to interrupt on both rising and falling edges and increases pulses per revolution from 20 to 40
2020-11-26 Implement feed-forward on speed controller - modified client to ask for minimum speed, as that is necessary for mapping a target speed to an initial pwm value for feed-forward behavior. - modified cl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
    [drive_wheel.cpp, drive_wheel.h, rover.cpp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]
2020-11-26 Send wheel id with speed control - speed control now takes a set of flags indicating which wheel(s) to apply the command. This is setup so we can keep individual speed control parameters for each whe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
2020-11-27 Add UI for individual wheel speed parameters The code prior to this update had a single set speed parameters that were used for both the left and right wheels/motors. However, the motors behave quite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
2020-12-05 Plot realtime motor telemetry in web client Added a bunch of code to take motor telemetry, publish it, buffer it and finally draw it to a canvas in realtime. - Implemented a system to read motor tele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
2020-12-14 refactor charts to include min/max speed setting - added a model singleton for the speed control settings so that other code would have access to them. I did it this way, rather than have other modul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
2020-12-18 Draw average speed on chart - A very important metric is the average speed over the last n milliseconds. We can use that when we are calibrating min and max speed for each motor and we can use it to 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
2020-12-18 Speed averaging window is configurable - added averageSpeedMs() to the Config singleton. - TelemetryCanvasPainter.paint() uses config.averageSpeedMs() when calculating the average speed for each whee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
2020-12-21 Plot pose telemetry - update pose calculation in TwoWheelRover._pollPose(). (x,y) still goes crazy when backing up over origin. Not sure why, but going forward seems to work fine. - To make sure that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
    [config.h, encoder.cpp, rover.cpp]
2020-12-22 Fixed bug in definition of encoder count props - the rover.h definition for _lastLeftCount and _lastRightCount were incorrect; they were unsigned int, which caused them to roll over when going in rev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
    [rover.h]
2020-12-27 Now queue up telemetry so sending does not block - Formatting and sending telemetry was previously in line with setting setting speed or pwm. This then would cause a delay while the telemetry was sen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
2020-12-29 Added noise reduction to speed and pose estimation - The velocity estimation in the pose and speed control methods were both prone to noisy data because of the low resolution of the optical encoder. 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
    [config.h, drive_wheel.cpp, drive_wheel.h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]
2020-12-30 Add command and UI to reset pose - we often want to reset the posed back to the origin when we start a second or subsequent run. Prior to this commit, that required restarting the rover and reloading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
    [rover.cpp, rover.h, rover_parse.cpp]
2020-12-30 UI to reset motor telemetry, fixed chart coords - Added a reset button to the motor telemetry chart. This just clears the telemetry listener data and resets the axis to defaults. There is not need to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
2021-01-04 Add images to README.md - starts a docs folder - added a couple of images of the web UI - added images to README
2021-01-17 Add Go To Goal behavior - The point of this commit is to add a working go to goal behavior. This is implemented in src/rover/goto_goal.cpp/.h as a class that calls the rover's public api to do it's w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
    [config.h, drive_wheel.cpp, drive_wheel.h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]
2021-01-18 Start button re-enable after go-to-goal finish - goto goal view controller now listens for goto-update messages and re-enables the start button on a NOT_RUNNING state. - rover's goto goal behavior no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
2021-01-30 Updates to encoder, stall value, forward value, documentation - fixed minor bug in telemetry.cpp:formatSpeedControl(); it was showing non-zero target speed even when speed control was turned off. Now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
    [config.h, drive_wheel.cpp, drive_wheel.h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]
2021-02-01 Added more encoder documentation
2021-02-03 Added documentation on ezrover wiring
2021-02-03 Small update to rover wiring docs
2021-02-03 Fixed issue #3; compile bug when disabling encoders - https://github.com/Ezward/Esp32CameraRover2/issues/3 - When build flags in platformio.ini were used to disable encoders and enable serial output,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
    [main.cpp]
2021-02-04 Added preprocessor symbol ENABLE_CAMERA - define ENABLE_CAMERA in platformio.ini to enable the camera - When it is NOT defined, requests for camera status simply return json with the 'enabled' proper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
    [camera_wrap.cpp, main.cpp]
2021-02-06 Hide camera UI if camera is disabled - There is a preprocessor symbol, `ENABLE_CAMERA`, that must be defined for camera support to be compiled ito the rover c++ code. By default in platform.ini the f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
2021-02-07 Fixed bug in encoding polling - if USE_ENCODER_INTERRUPTS is not defined, then the rover C++ code using polling rather than interrupts to read the encoder input pins. - There was a bug that causes th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
    [encoder.cpp]
2021-02-22 Fix Arduino.h in platformio.ini - capitalization of Arduino.h was wrong in platformio.ini, so this caused build failures in linux. MacOS and Windows were not affected because their file systems are c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
2021-03-03 Added info on 3d printed camera mount
    [Esp32Cam_gopro.stl, gopro_rover_base.stl]
2021-11-02 fixed section link
    [below](#reducing-noise-in-velocity-measurements)
2022-06-09 Update utilities.js
    - refactor isValidNumber so it can check for > max without having to check min range
    - refactor filterList so check that filterFunction is a function.
